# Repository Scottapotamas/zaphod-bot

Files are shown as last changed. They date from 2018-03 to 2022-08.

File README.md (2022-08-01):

# ZaphodBot Lightpainting Robot

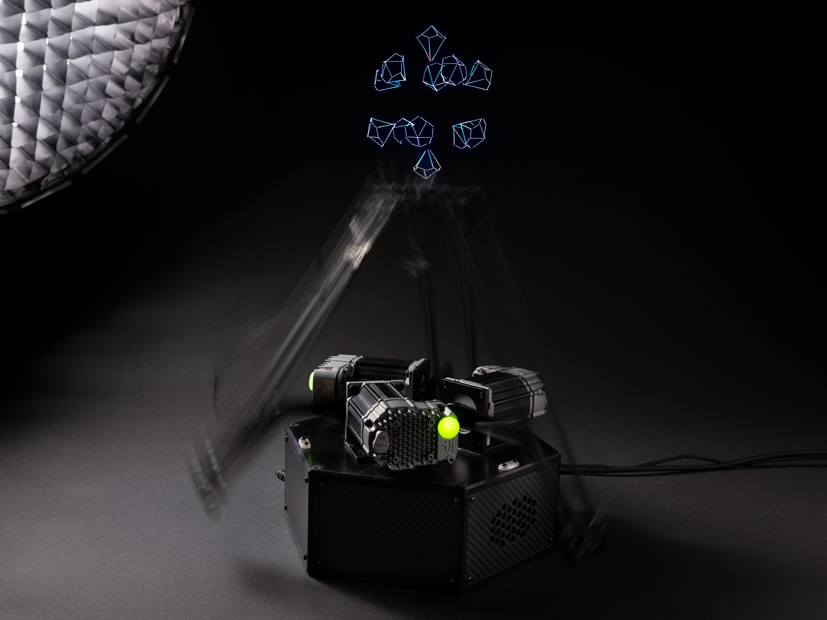
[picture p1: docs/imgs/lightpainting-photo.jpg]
lightpainting-photo


ZaphodBot is a DIY, 'high-end' rotary delta robot designed primarily for high-fidelity light painting.

It's served as a personal project where the majority of mechanics, electronics, firmware and higher level software has been designed from scratch (because why not).

I've detailed the design motivation and build in a more [longform post here](https://electricui.com/blog/delta-bot).

## Mechanics

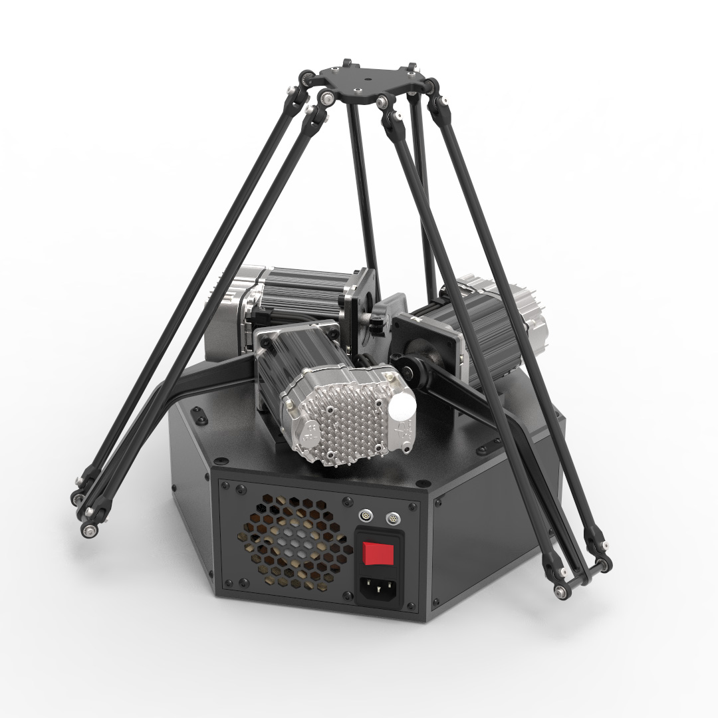
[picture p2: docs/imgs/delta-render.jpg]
Render of V1 Delta Hardware


CAD files for the robot are in Solidworks 2015 format, and can be found in `/mechanical/design/`.

The power supply and main electronics stacks live inside the hexagonal structure which forms the base, with servos mounted on top, connected directly to the arms.

To manufacture parts, see `/mechanical/design/manf_outputs/`  for drawings, STEP/DXF files. SLA 3D printing was used for joints, and CNC machining for the aluminium parts and carbon plates. 

All fasteners are standard metric hex bolts, with the exception of some bottom mounting holes which are 1/4in and 3/8in threaded holes to suit typical camera tripods.

## Electronics

The PCB was designed using KiCAD 5, located in `electronics/zaphod-controller`. Gerber outputs are available with BoM, but minor design revisions are needed to improve wire-loom layout and debug/expansion connector positions. 

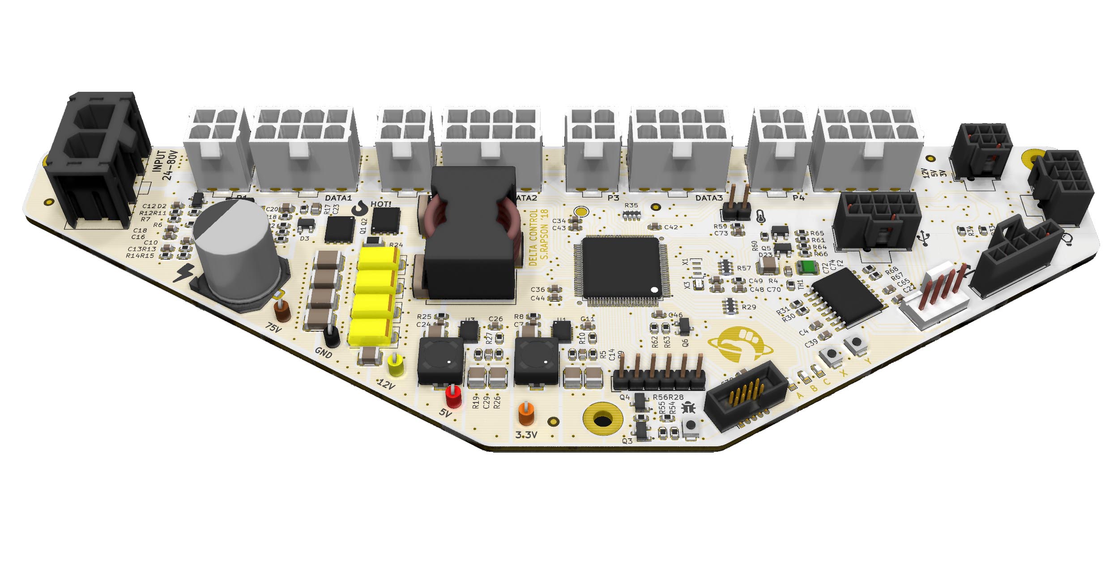
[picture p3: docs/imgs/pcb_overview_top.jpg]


It's based on a STM32F4 processor, provides regulated 3/5/12V from the 75V system supply, and manages the servos, internal IO and external IO.

- Power input (75V from Teknic IPC) through 2-pin MOLEX SABRE connector.
- Clearpath servo motors connect with 8-pin MOLEX MicroFit for signalling, and 4-pin MicroFit for 75V supply.
- Internal IO NanoFit connectors provide PWM fan support, UART, I2C, 2x ADC/DAC, and PWM. These can also be used as generic IO. See  `/electronics/zaphod-controller/Outputs/zaphod-controller-sch.pdf` for pinouts.
- Internal IO 2.54mm header strip provides switchable+fused 3.3V and USART, intended for wireless comms backpack in the future (likely ESP32 flavoured).
- The 9-pin LEMO connector used for external expansion provides galvanically isolated USB and 4 isolated IO lines (2 inputs, 2 outputs). Pinout in `/docs/connectors_pinouts.md`.
- The 7-pin LEMO connector supports a 4th Clearpath SD series servo, intended for use with rotating or linear stages. Pinout in `/docs/connectors_pinouts.md.`

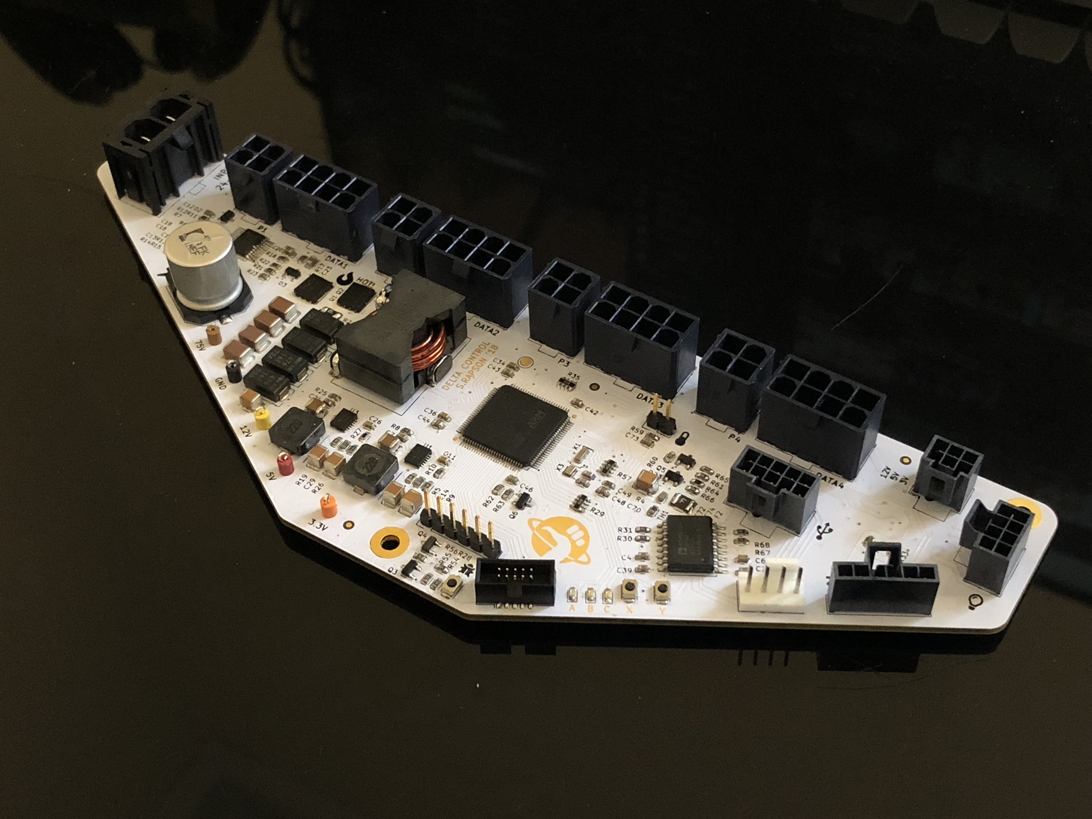
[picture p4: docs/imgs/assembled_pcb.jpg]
Assembled PCB


## Firmware

Microcontroller firmware (STM32) is in `/firmware`, is written in C, and can be built with a fairly standard `arm-gcc-eabi-none` toolchain.

I've used (and included config for) CLion as my main IDE, which is CMake based, though building with SW4/Eclipse shouldn't be too hard either.

Flashing the microcontroller is pretty standard as well, a 10-pin ARM CORTEX SWD socket is on the PCB, which connects to a STLink, Blackmagic Probe, or JLink programmer (used all three at various stages of this project).

# User Interface

The user interface is built with [Electric UI](https://electricui.com/install), and can be built and run by invoking `arc start` from `/interface`. 

It facilitates control and monitoring of the hardware, along with toolpath generation, optimisation and visualisation pipelines.

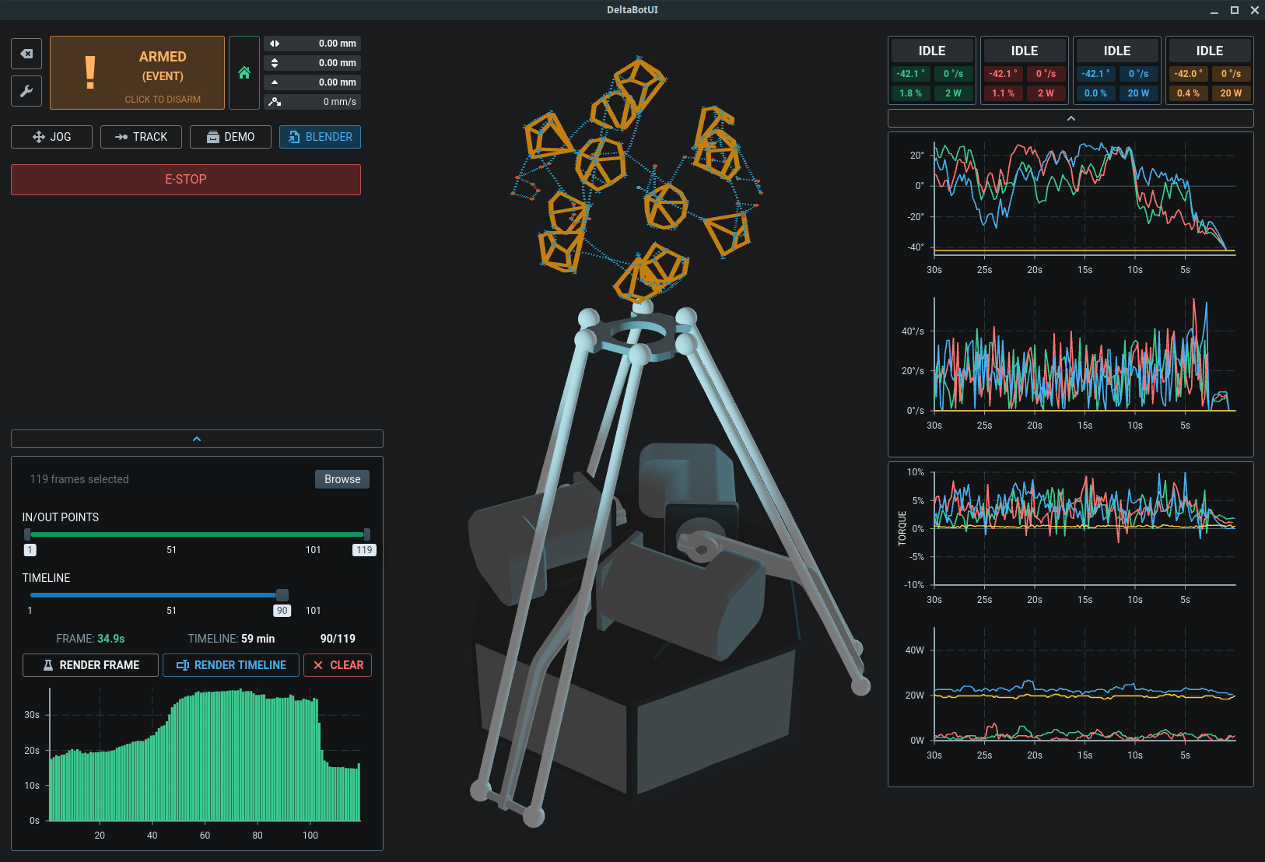
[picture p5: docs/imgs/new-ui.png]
User interface


## Toolpath Generation

Toolpaths for lightpainting are created by exporting spline data from [Blender using a Python script](https://github.com/Mike-Dax/total-perspective-vortex/blob/main/blender/addons/total_perspective_vortex/tpv.py), and loading the output with the "Blender" tab in the UI.

The frontend UI is responsible for parsing the Blender scene and performing a series of move planning and TSP optimisation steps to reduce render times.

https://user-images.githubusercontent.com/460325/182141536-1118c95f-b80b-4199-9833-aa961b41ea9a.mp4

> This screencap shows a Blender animation being loaded: the 'fast' plan completes within a second, then the multi-threaded TSP solver iterates on each frame to refine the path taken to render the particles.

# Accessories

## Light Painting

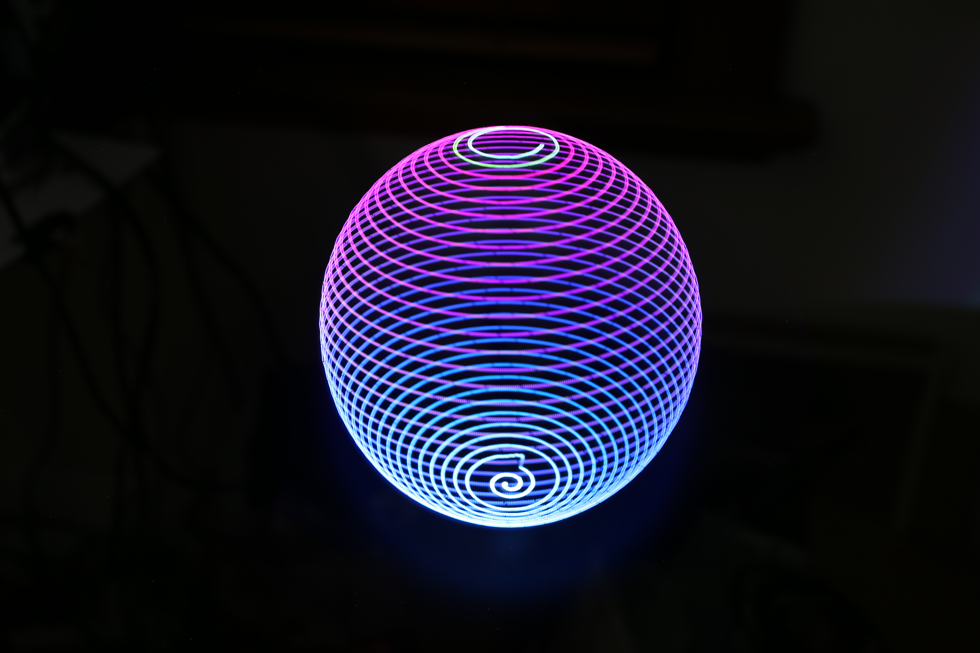
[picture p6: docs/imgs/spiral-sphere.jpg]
Light-painted spiral sphere


The light-painting 'brush' uses acrylic 1mm core fibre, connected to a 3x3W RGB LED.

The fibre is mounted to the effector with a turned acetal stalk (not documented), or with one of the SLA printed mounts found in `/mechanical/fibre-couplers/`.

The driver PCB is in `/electronics/rgb-led-board/` along with manufacturing files and a simple Arduino test program. This board connects to `zaphod-controller` via the 8-pin NanoFit connector, which provides PWM+IO and power.

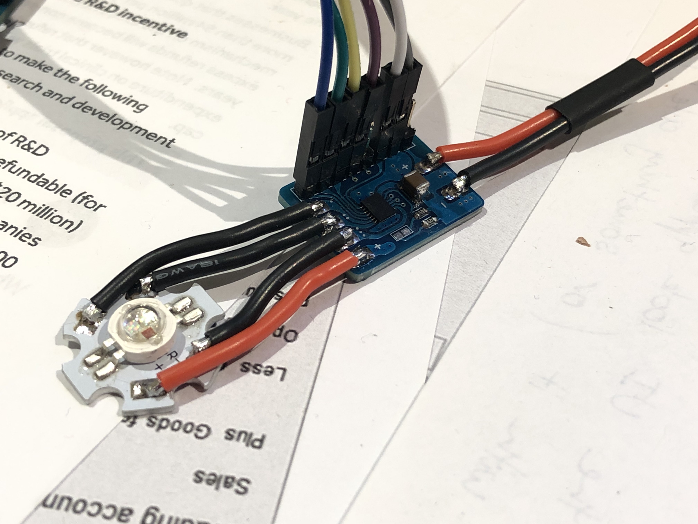
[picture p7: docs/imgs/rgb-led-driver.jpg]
RGB LED driver


## External E-STOP + IO Breakout Box

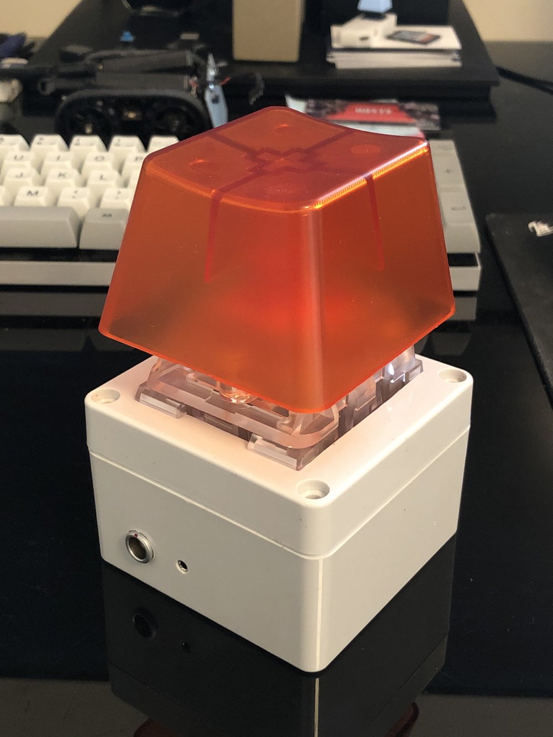
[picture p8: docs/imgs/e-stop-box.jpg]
E-STOP Box


The 9-pin LEMO connector is used with a 2m cable, connecting to the breakout box via matching 9-pin LEMO. A [Novelkeys Big Switch](https://novelkeys.xyz/products/the-big-switch-series) is used as an E-STOP, with the keyswitch light indicating motor state.

A 2.5mm stereo socket mounted in the box provides support for camera shutter release cable, in this case for a Canon N3 connector.

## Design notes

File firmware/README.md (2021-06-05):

# Embedded Firmware Readme

STM32F4 firmware for the zaphod-controller PCB. Manages the delta's servos and handles movement processing.

Uses the ST LL (LowLayer) hal as a base, with my own HAL on top of (or replacing) as applicable. Written for the STM32F429VET6 target microcontroller.

General system runs with event driven HSM design patterns, while background tasks use somewhat simple statemachines to handle operation.

## Building

Uses the `arm-gcc-eabi-none` toolchain, should build with fairly standard flags.

The external deps `electricui-embedded` and `electricui-interval-sender` use git submodules, and are both CMake aware.

`clang-format` config file is under git, used to maintain some semblance of style consistency.

GitHub Actions workflows are setup to build firmware in debug mode on commit to master, and release builds when tagged. Look at the Releases page on GitHub for binary downloads.

## Flashing and Debugging

I use CLion as my IDE alongside a JLink.

Depending on the version, either run a remote GDB server, or use CLion's integrated support.

### Manually running GDB server

Run the JLinkGDBServer as the remote GDB server instance with 

`./JLinkGDBServer -if SWD -device STM32F429VG`

then in CLion, connect with a remote GDB debugger with target-remote args of `tcp:localhost:2331`.

I had to edit my `~/.gdbinit` to include flashing and reset commands, which looks something like this:

```
# Reset the chip to get to a known state.
define target hookpost-remote
load
monitor reset
monitor halt
b main

# Set auto JTAG speed
monitor speed auto
```

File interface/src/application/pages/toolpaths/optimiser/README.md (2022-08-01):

# Colors

All colors are unit colours internally, RGB 0-1 values.

# Materials

Materials can't have any effect on the ordering of the movements.

## Blender Materials

Materials support arbitrary data transfer. Any `Object Data` custom properties
with the prefix `material.` will be transfered into the `material` entry without
the prefix. We use the `Object Data` custom properties because that usually
makes more sense with the object. GPencil and Lights are supported

Eg: to use the rainbow colour:

`material.type`: `rainbow`

Or a regular colour material

```
material.type: color
material.color: [1.0, 1.0, 1.0, 1.0]
```

Python syntax dicts can be entered for complex data structures

```
{'type': 'color', 'color': [1.0, 0.087, 0.05]}
```

Dot notation string keys can be used to override specific members (for use with
drivers)

```
material.foreground = {'type': 'z_depth', 'color_from': [1.0, 1.0, 1.0], 'color_to': [0.0, 0.0, 0.0], 'depth_from': 950, 'depth_to': 1000}
material.foreground.color_from = [0,0,1]
```

{'type': 'z_gradient', 'z_from': 105, 'z_to': 180, 'color_from': [0.360784,
0.145098, 0.360784], 'color_to': [0.760784, 0.454902, 0.760784]}

## Empty special data export

Custom properties of empty objects with the prefix `frame.` are exported, minus
the prefix, into the frame metadata store.

`frame.exp_angle` for example becomes `exp_angle` which is used to control the
4th axis.

## Drivers

Any property can be 'driven' by any combination of math, python scripting, and
other properties.

Right click -> `Add Driver` to add a driver.

# TODO:

- DRY the threejs representation into a simple colour interpolator
- BlendMaterial that can operate over two materials, multiply / min / max
- Z Fade material that fades 0 - 1 based on distance to camera near and far
- Fuzz material that can vary lighting intensity
- Some way to multiply light intensity with speed

- Motion fuzziness?

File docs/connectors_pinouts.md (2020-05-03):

# Connectors and Looms

General overview of components required for power delivery and signalling.

The main PCB will provide distro and sensing (voltage & current sense per motor) as well as IO connections.
This should hopefully keep the wiring neat and professional (looking, at least).

I'd like to sleeve each wire/bundle as well, but we'll see how much time I have.

# Mains Input Connection

Connect output of holder to IPC-3/5 PSU.

### Parts

- IEC320 Connector 	- Fused with DPST switch (no backlight). 
- Spade Terminals	- Female, fully shielded terminals. 
- Ring Terminal 	- for grounding connection(s). 
- 240IEC320V Fuse 	- M205 Quick Blow Fuse 4A. 

https://www.jaycar.com.au/iec-fuse-chassis-male-power-plug-with-switch/p/PP4003
https://www.aliexpress.com/item/AC250V-10A-2pin-ON-OFF-Rocker-Switch-IEC320-C14-Inlet-Socket-Single-Fuse-red-Switch-black/32861211516.html

Spade crimps - Potentially dubious quality, but better than the unshielded ones I have on hand...  
https://www.aliexpress.com/item/Lowest-Price-30PCS-Yellow-red-blue-Splice-Wire-Connectors-Insulated-Male-Female-Crimp-Spade-Terminals-18/32764325209.html

### Wire

Preferably in black insulated (round):

- 2.5mm^2		Blue
- 2.5mm^2		Brown
- 2.5mm^2		Green/Yellow

### Pinout

- Active is connected directly to the fuse holder on the IEC connector. 
- Connect the fused active to the switch. 
- Connect the switched active to the IPC active connection. 
- Neutral directly to IPC neutral pin. 
- Earth directly to the IPC neutral pin. 

# Teknic IPC-3/5 Open Frame PSU

## Mains Input connector

Connect to input protection circuit(s).

### Parts

- Molex MiniFit-Jr 	8-Way - 39-01-2080
- Molex MiniFit-Jr	Crimp - 39-00-0039

### Wire

From IEC switch unit (2.5mm^2 3-core).  
This was cut from an older black 240-IEC cable.

### Pinout

- Pin 1-4 	No Connect for 230V, read manual for 110V operation
- Pin 5 		AC Active
- Pin 2 		Earth
- Pin 2 		Earth
- Pin 8 		AC Neutral

## 75 Output Connector

- Connect IPC-3/5 Output to main PCB.  
- The PSU and the PCB use common connector and pinout.
- This is also listed in the Teknic IPC User manual PDF.

### Parts

- Molex Sabre 		2-Way - 44441-2002 
- Molex Sabre 		Crimp - 43375-0001

### Wire

- 14-16AWG 	Red
- 14-16AWG 	Black

### Pinout

- Pin 1 		VCC
- Pin 2 		GND

# Teknic Clearpath Motor(s)

I bought ModDIY pre-crimped mini-fit cables to reduce the labour of individually sleeving these.  
In hindsight, I should have provisioned a panel mount connector for the top plate, and had the full looms made up (including connectors) as the ModDIY cables had thick heatshrink that interferes with insertion into the housing, taking as long/longer than full DIY cables...

## Power Connector

- Connect motor power to the main PCB.
- Motor and PCB share common pinouts, connectors etc.

### Parts

- Molex MiniFit-Jr 	4-Way - 39-01-3045
- Molex MiniFit-Jr 	Crimp - 39-00-0078

https://au.rs-online.com/web/p/pcb-connector-housings/6704575/  
https://au.rs-online.com/web/p/pcb-connector-contacts/2155887  

### Wire

- 16AWG 		Red
- 16AWG 		Black

### Pinout

- Pin 1 		VCC
- Pin 2 		GND
- Pin 3 		VCC
- Pin 4 		GND

## Control Connector

- Connect clearpath data connector to main PCB.  
- Motor and PCB share common pinouts, connectors etc.  

### Parts

- Molex MiniFit-Jr 	8-Way - 39-01-3085
- Molex MiniFit-Jr 	Crimp - 39-00-0078

https://au.rs-online.com/web/p/pcb-connector-housings/8428197/
https://au.rs-online.com/web/p/pcb-connector-contacts/2155887

### Wire

- 22AWG 		Blue
- 22AWG 		White

### Pinout

- Pin 1 		HLFB+
- Pin 2 		Input B+
- Pin 3 		Input A+
- Pin 4 		Enable+
- Pin 5 		HLFB-
- Pin 6 		Input B-
- Pin 7 		Input A-
- Pin 8 		Enable-

The PCB connects the + signals to the common 12V rail, as signalling is done on the low side.

# Expansion LEMO Connectors

## Data Connector

Allows for user-domain expansion of USB and some generic IO (UART, CAN, 2x input, 2x output).

### Parts

LEMO 0B 9-pin

Socket: EGG-0B-309-CLL
https://au.mouser.com/ProductDetail/LEMO/EGG0B309CLL

Plug: FGG-0B-309-CLAD-52Z
https://au.mouser.com/ProductDetail/LEMO/FGG0B309CLAD52Z

As a pair (off-brand equiv): 
https://www.aliexpress.com/item/LEMO-connector-EGG-0B-309-CLL-FGG-0B-309-CLAD-Z-31Z-42Z-52Z-LEMO-connector/32318767655.html

### Wire

USB3		Black Sheath

Usb cable provides 9 usable conductors (not counting the shield), with good shielding, and compatible diameter with lemo sheath.

Black glue-lined 6mm heatshrink was used to protect the joints on the panel mount side.

### Pinout

When looking at the back side of the LEMO panel mount connector (wire side), with the alignment notch facing up.
The pin pattern is defined where pin 1 is the pin directly underneath the alignment notch, counting upwards in a counter clockwise direction, and pin 9 is the centre pin.

```
     1      
  2     8   
 3   9   7  
  4     6   
     5     
```

'Legacy' USB FS Connection:

- Pin 1 		GND 	BLACK
- Pin 2 		D+		GREEN
- Pin 3 		D-		WHITE
- Pin 4 		5V		RED

IO Group 1 (CAN Capable):

- Pin 5 		In/RX	BLUE
- Pin 6 		Out/TX 	YELLOW
- Pin 9 		IOGND	BARE (in pair shield)

IO Group 0 (UART Capable):

- Pin 7 		In/RX	PURPLE
- Pin 8 		Out/TX 	ORANGE
- Pin 9 		IOGND	BARE (in pair shield)

IO and USB don't share ground. The two IO groups share ground cores as the PCB joins them anyway.

### Notes

- The USB3 insulation diameter just fits inside the LEMO strain relief jacket. This required a bit of force, and some slight lubrication of the wire.
- The USB Shield connection (outer copper core, and woven+foil shield) was not electrically connected at the lemo plug/socket side.
- Hot air gun was used to slightly soften the panel-mount -> PCB loom to allow bending. These bends are reasonably well retained after cooling.

## Motor Connector

Allows for addition of an external clearpath motor (or something that uses the same IO style)

### Parts

LEMO 0B 7-pin

Socket: EGG-0B-307-CLL
https://au.mouser.com/ProductDetail/LEMO/EGG0B307CLL

Plug: FGG-0B-307-CLAD-52Z
https://au.mouser.com/ProductDetail/LEMO/FGG0B307CLAD52Z

As a pair (off-brand equiv): 
https://www.aliexpress.com/item/LEMO-connector-EGG-0B-307-CLL-FGG-0B-307-CLAD-Z-31Z-42Z-52Z-LEMO-connector/32318771454.html

### Wire

N/A

### Pinout

```
  1     6   
 2   7   5  
  3     4   
```

- Pin 1 		75V 	RED
- Pin 2 		12V		BROWN
- Pin 3 		ENABLE	BLACK
- Pin 4 		A		BLUE
- Pin 5 		B		GREEN
- Pin 6 		HLFB 	ORA
- Pin 7 		GND 	YELLOW

### Notes

- The 7-pin connector was selected for unique pin count, higher supported wire gauge (and higher per-pin current).
- Not intended for continuous high power delivery to motors, mostly for use with rotation or belt surfaces, or possibly rail drive.
- Connector pins are rated at 2.5A continuous.
- Isolation rating of connectors is >700V, therefore 75VDC is fine.

# Expansion Temperature Probe

Used for temperature sensing off the main control board. 

Recommended location is inside the warmer area of the IPC-3/5 PSU to allow for automatically moderated airflow.

### Parts

10K NTC Thermistor  
https://www.aliexpress.com/item/10K-Precision-Epoxy-Thermistor-3435-NTC-Pack-of-2/32819250168.html

2-pin 2.54mm pitch 'DuPont' connector

I sleeved and heatshrinked over the plug. The thin nylon wires were a pain to manage.

### Wire

Thermistor already comes pre-wired.

### Pinout

It behaves as a resistor, pinout doesn't matter. 

Crimp both terminals into the 2-pin socket, connect to temp header on PCB.

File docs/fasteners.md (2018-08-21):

# Version 1 Fasteners

## Bearings

4mm ID, 4mm depth, 9mm OD

Instead of paying $5 each (x24), I found some on aliexpress

https://www.aliexpress.com/item/Free-Shipping-10-PCS-S684ZZ-Bearings-4x9x4-mm-Stainless-Steel-Ball-Bearings-DDL-940ZZ/32835314182.html

Bearings seem of reasonable quality, centre retainer is slightly looser than I'd like.

## Shoulder bolts

There are two shoulder lengths required, 4mm for effector and bicep connections, and 8mm for use with the clevis links.

I went with the cost effective aliexpress option https://www.aliexpress.com/item/10pcs-M3-thread-4mm-stainless-steel-304-shoulder-screw/32861370400.html

4mm and 8mm skews were purchased.  
They seem dimensionally undersized for the shoulder diameter (3.85-3.92mm shoulder).  
Hex head forming seems a bit rough.   
Otherwise seem ok though.  

### Steel slotted variant

4mm shoulder, 4mm shoulder length, M3x0.5
4.5mm thread length
Carbon steel

SHLD040-004-SLL-C - $1.95AUD each

https://www.minibearings.com.au/store/item/shld040004sllc/

### Stainless Hex variant

4mm shoulder, 4mm shoulder length, M3x0.5
303 Stainless Steel
4.0mm thread length

SHLD040-004-SKT-S3 - $3.95AUD each

https://www.minibearings.com.au/store/item/shld040004skts3/

### Stainless Hex variant

4mm shoulder, 8mm shoulder length, M3x0.5
303 Stainless Steel
4.0mm thread length

SHLD040-008-SKT-S3 - $3.95AUD each

https://www.minibearings.com.au/store/item/shld040008skts3

# Version 2 Mechanism

The version 1 mechanism has way too much slop due to poor tolerances in the bearings and shoulder bolts. Good lesson in not trusting Aliexpress fasteners...

This set will use higher quality fasteners from Misumi, but requires a few parts to be reprinted.

## Bearing Retaining Posts

Without re-machining or redesigning the elbow spacer part, I'm limited to a M3 thread.

The "Bearing Shaft Screws with Retaining Rings - Flanged" look pretty good, https://sg.misumi-ec.com/vona2/detail/110300115260/
or a simpler option that don't have a retainer (basically a shoulder bolt) https://sg.misumi-ec.com/vona2/detail/110302644720/

The M3 thread size in these categories locks us into a 5mm diameter which drives bearing selection.
Its got a 6mm thread length, and 8mm head

## Bearings

Inner Diameter: 5mm
Outer Diameter:	11mm
Width:			5mm

The misumi branded stainless steel shielded bearings https://sg.misumi-ec.com/vona2/detail/110302273360/?HissuCode=SB685ZZ look like a good option. Its 3.60USD at qty 26 (need 24 + 2 spares) 

94.64USD.

## Clevis Bearing Pin/Shaft

TBD, misumi have poor selection of ~10mm options, most start at 15mm shank which isn't ideal.

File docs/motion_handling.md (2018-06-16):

# Motion Handling

Summary of the motion planning setup.

## Work Area

The main co-ordinate system is represented as a cartesian space, measured in microns. This allows for use of int32 x, y, z numbers with sufficient resolution and spare room for rails etc.

The XY plane is defined as the plane parallel to the main hexagonal plates of the delta, with the 0-point of XY being co-linear with the central vertical axis of the bot (centre of plate, motor axis etc). The Z axis is defined as the vertical distance from the delta, where the '0' position is the closest reachable point to the delta's base electronics assembly (i.e. arms are about to hit endstops). Positive Z positions are away from the robot, moving towards the fully extended range of motion.

## Motion Processing Pipeline

Movements can be specified as one of several types, a transit, line, or one of several spline choices (catmull rom, quadratic bezier, cubic bezier). 
Points are passed to the pathing engine to generate the lines or splines, in micron-resolution x,y,z cartesian format.
A 'target duration' is specified for the movement, where the delta will attempt to complete the move by the elapsed duration.

While executing a movement, the pathing engine will calculate the time elapsed since the start, and calculate the percentage of completion required.
The end-effector's position is calculated using the appropriate line or spline interpolation function, with the percentage as the dependant variable.
The output co-ordinates are then fed into the kinematics driver, which performs the inverse kinematics required to translate the cartesian co-ordinates into motor angles.
On successful IK solve, the motor angles are sent to the clearpath handlers, which convert the target position into steps, and manage the actuation of the servos.

By repeating this process often, movement along a path can be achieved with some level of accuracy (assuming the servo motors can maintain control to meet the setpoint).
As the processing stages require a non-zero amount of compute time, the number of 'subdivisions' achieved by the pathing engine is dependant on the time allowed by the movement.
Therefore, large fast moves have lower resolution than either smaller fast moves, or large slow moves.

## Servo Angles

When the servo homes, it moves to an endstop which correlates to a bicep angle of -65° (where 0° is parallel to the plate). 
The motor then moves 150 steps from this point as a 'buffer', or to -56.5°.

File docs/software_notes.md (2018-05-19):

# Architecture Overview

There are a few layers of abstraction which make up the overall structure of the firmware.

| Folder 				| Description  	|
|---				|---			|
| app_state_machines 	| HSM structured higher level logical tasks. Subscribe and emit events. Only allowed to interact with drivers. 										|
| drivers 				| Simpler self-contained modules, some contain a simple-state-machine implementation. Typically manage hardware, convert sensors to quantities etc.  	|
| hal 				| Hardware abstraction to interact with specific peripherals or microcontroller functions.  															|
| utility 				| Helper code which forms the backbone of the statemachines, or some other generic behaviour (fifo, queues, state machine macros).  					|

The hal layer provides convenience wrappers for other lower level functionality, be it direct register calls or interfacing with the STM32 HAL layers.

The intent of 'my' hal layer sitting above the STM32 HAL is to further decouple the code from the STM ecosystem, which improves testability and reuse of drivers.

## Tasks (HSM)
 
Based on a hierarchical state machine structure (HSM), which provides event-driven state machines called 'tasks'.  
Found in /src/app_state_machines

Event timers are evaluated on a tick timer (along with ADC or other timing specific modules).  
The main loop sleeps wherever possible, waking on interrupt. At this point, the background processors are visited, then a task from the queue is run.  
For a given 'task', an arbitary number of states can be defined (as functions), which contain a macro driven pattern for handling entries and exits from the state, and handling for external events.

## Drivers
 
Simpler blocks designed to operate statelessly or with a simple state machine and processing loop. These aren't handled by the task systems, and aren't intended for complex logic.
Found in /src/drivers

Drivers should expose public facing functions for init, getters and setters, and processing 'loops' if required.  
A driver will typically perform a role where interaction with the HAL layer is required, such as sampling a ADC, i2c sensor, or drive a PWM output, and typically provides human-friendly interactions with the underlying hardware.  
ADC or sensor readings should be converted into a SI unit for example, and averaging/bounds/error detection should be done at this layer.

## hal

Interacts with the hardware on a more generic level. This may be direct hardware register manipulation, or calls to a vendor HAL codebase.  
Found in /src/hal   

hal code should strive to abstract the operation of the bare metal to simplistic actions such as start/stop/action, and should attempt to consolidate settings for peripherals.  
This is designed to allow the driver layers to be unit tested independantly of hardware, as the hal layer can be mocked.  
Also promotes portability as the hal layer can be changed subtly for new vendor IC's as needed.

## utilities

Provides standard functionality used across driver or task layers, includes functionality like queuing, state handling or buffer style functions.
Found in /src/utilities  

Many modules consist of defines or macros to simplify the higher layer.  
Where possible, these are as generic as possible.

# Delta Notes

General overview/thoughts regarding firmware development for the controller. These might be as simple as listing the responsibility of certain modules.

## Fan Control

The fan driver presents a simpler loop run in the background at a lower-rate.  
Interacts with the hal PWM to set fan speeds, and monitor the fan hall sensor and temperatures.  

Handles starting/stopping the fan with a blip to higher speed to ensure safe starting.  
Includes stall detection and underspeed detection, attempts to restart.  
Monitors the temperature and tracks a fan curve for auto-speed.  

## Kinematics 

The kinematics driver provides transforms between the cartesian co-ordinate space, and angular roations for each motor.

Forward Kinematics (angles to position) and Inverse Kinematics (position to angles) are available.
Functions take a structure for either position or angles as input, with a pointer to a writable structrure (output) of the other type.

Bypassing this module would allow use of the overall motion planners etc for different mechanisms (SCARA, cartesian, etc)

## Path Interpolator

Driver operates in the cartesian domain only, and is designed to accept a 'motion request' and then execute the motion over some duration of time.  
As movement to a destination isn't as simple as driving motors to the final destination instantly (co-ordination is required for correct temporal profiles, kinematics considerations etc), we need to calculate a target position for the end effector at a given time, then calculating the intermediary movements to provide speed/duration control etc.  

To ensure the effector follows the target profile over time, the motion is broken up into smaller chunks. Greater number of chunks provides greater adherance to the intended profile.  
As the delta is intended for use against temporal problems, the movement engine was designed around the concept of 'time domain' movement execution, not feed rate based moves like many CNC machines.  

As such, each movement has a corresponding 'duration', and the interpolator driver strives to complete the movement within this time window.  
By adjusting the rate of the interpolator's loop, the fidelity of the movements is then traded against movement speed.  
A large and small movement which share execution durations will recieve a similar number of chunks, and therefore positional adherance will vary.

Tool-positioning calculations depend on the style of motion requested, and several interpolation functions are included to assist with this:

### Transit movements

Transit movements are used where the 'where' matters more than the 'how', and will execute without any guarantee of the tool path between points.

For the delta, the end effector position along this transit move will be influenced by the non-linear relationship of the mechanics and motor angles.

### Line Movements

Linear interpolations are used to perform line following between 2 3D points.

### Spline Movements

Catmull-Rom Spline interpolations are used to follow a segment of the curve defined by 4 points.

https://en.wikipedia.org/wiki/Centripetal_Catmull-Rom_spline

The higher level task, or the movement generation tool can generate large chains of points to ensure all waypoints are hit.

### Arbitary Equation Moves

Not currently implemented.

The ability to accept an arbitary mathematical function is a wanted feature? 
Could be cool to provide arbitary spirographic functions for demos.

## Clearpath Driver

Handles the homing and control of a single servo.
Monitors current and feedback pins to approximate some failure detection/prevention.

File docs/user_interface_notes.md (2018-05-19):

# Delta Robot User Interface

General musings and tracking of user interface development.

## Overall System

| Group 	| Component 	| Task 	| Implemented 	|
|---	|---	|---	|:---:	|
| Fan Control  	| Speed % 	| Show current duty cycle 	| 	|
| 	| Speed RPM 	| Show current RPM 	| 	|
| 	| Fan Curve 	| Allow edits of temp/speed curve 	| 	|
| Temperatures 	| PCB Ambient 	| In open-air part of PCB 	| 	|
| 	| PCB 12V Reg 	| Underneath 12V regulator 	| 	|
| 	| External Probe 	| Flying probe (near 75V PSU) 	| 	|
| Motion 	| Status 	| Idle, homing, transit, line, spline, etc  	| 	|
| 	| Cartesian Pos 	| (X, Y, Z) in 20.05mm format 	| 	|
| 	| Angular Pos 	| Shaft angles in 34.5° format 	| 	|
| Status 	| System State 	| Overall hardware status 	| 	|
| 	| LED 0 	| Indication matching onboard leds 	| 	|
| 	| LED 1 	| 	| 	|
| 	| LED 2 	| 	| 	|
| 	| Button 0 	| State of button presses (accept UI press) 	| 	|
| 	| Button 1 	| 	| 	|
| 	| CPU Load % 	| Utilisation Stat 	| 	|
| 	| Micro Core Temp 	| Internal temperature sensor 	| 	|
| 	| Add-in card state  	| If add-in card is powered or not 	| 	|
| 	| Buzzer state 	| If buzzer is currently indicating or not  	| ? 	|
| Motor X 	| State 	| Passive, Homing, Idle, Motion, Error 	| 	|
| 	| Feedback Signal 	| -100% to +100% value for velocity/torque  	| 	|
| 	| Current Position 	| Internal tracked current position 	| 	|
| 	| Target Position 	| Servo driver target 	| 	|
| 	| Power 	| Consumption in Watts 	| 	|
| 	| Current 	| Draw in 1.25A format 	| 	|
| 	| Current Fault Flag 	| Indication from sense IC of OC event 	| 	|

# UI Components required

The UI will require the following generic data driven components:

- Graphs (continuous display of live values).
- Statistics/Labels of data.
- Indicator 'lights' for button and status led indication.
- Fan curve viewer/editor.
- State Indication (text mapper from int -> strings).
- Notifications/alerts
- Mode Selection Module.
- Emergency stop button.

- Visualiser of end effector position/trail in cartesian space.
- Visualiser of delta mechanism with movements (either do IK or FK at UI side).

These elements will require grouping to improve readability, and dropdowns, tabs or navigation required to expose all information.

For example:

- Dropdown/tab in isolated box to select between motor overviews, and Servo 1-3 detail status.
- Grouping of status values, temperatures and state information.
- System stats like CPU load and microcontroller core temperature on a separate page or footer element.

Some states will flag critical issues or confirmations, and these should require either an OS level notification, in-app banner, or challenge dialog.

## Mode Selection Module

Allow selection between operation modes: Manual control, demo sequences, run program, accept serial

### Manual Mode 

Direct user input of motion controls.  
Suggest ability to toggle which input method is used:

- UI entry (sliders/buttons that fire a fixed amount of movement per press).
- Mouse/touchpad control (xy control in a box).
- Joystick control (bluetooth or connected gamepads).
- Spacemouse Control (attached to the UI/host computer).
- Manual entry of position as x,y,z fields, in mm.

### Demo Mode

Run through preset motion demos to show off the control accuracy and velocities of the delta.

Concepts include:

- Tracing out simplistic 2D geometry.
- Trace out 3D cube edges.
- Spiral and cone style patterns.

### Program Mode

UI presents interface for file selection.  
Either microcontroller stores the file, then runs, or the UI feeds motion commands piecemeal.  
Shows progress indication bar.  

### Serial Mode

Accept control inputs from external connection and other devices.  
This allows the UI to be used as a supervisor.

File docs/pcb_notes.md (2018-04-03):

# Main Interface PCB

Purpose: Accept inputs, provide output connectors, maintain wiring and provide high level control over system.

Side Goals: Look awesome.

# Requirements

## Input

- Accept 75V DC from IPC-3 PSU with 2-pin Molex SABRE connector.
- Minimalistic input protection and filtering as supply is trustworthy.
- Polyfuse, a few caps for stability?
- Input voltage test points

## Processing

- Accept input position data at high rate (USB, Ethernet, Wifi, SD/USB are all acceptable).
- Drive 3 stepper motors at high speed, i.e. maximum achievable square waves for ultimate positioning control
- Drive 1-n RGB LEDs for output
- External optocoupled IO for inputs/soft stop switch, and camera trigger events.
- Should be able to handle reasonably involved trig/floating point maths for kinematics calculations.
- External outputs for end affector upgrades in the future
- Inputs for homing switches
- Buzzer output for safety alerts?

## General nice-to-haves

- Onboard NTC for temperature monitoring
- Expansion NTC's to monitor IPC-3 power supply temperature, etc.
- PWM Fan output for cooling
- Consider input voltage, and current sensing on each servo output rail.
- SWD Connection with ARM CORTEX 5x2 pin female 1.25mm pitch.
- Ensure high reliability, robust IO and isolate where practical.
- Expansion PWM outputs for end affector upgrades/changes in the future (pumps/servos etc)
- Expansion UART and/or CANBUS for external interfacing.
- Terminal over UART is nicer than USB for debugging.
- Testpoints for scope/function generator
- TTL level lines could use 2.54mm 4x2 connectors for Saleae logic analyser connection (step+dir+enable+hlfb).
- Consider onboard RTC battery connection.
- Connection for ESP8266/32 for wireless expansion?

- Matte-black PCB with ENIG finish. Gold text etc.
- Use only Orange or Blue LEDS for indication
- Leds should be low brightness or include disable functionality.

## Outputs

- 3x Motor Connectors (power + control connectors)
- Status/state LEDS on important pins for visual debugging.
- External UART
- External USB
- External IO

- Bonus for 4th motor output if 4th axis expansion is considered

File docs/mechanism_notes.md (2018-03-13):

# Delta Mechanism Design

Goal is for a high speed, high resolution, low load actuator in 3-dof space.

- Ideally the platform has minimal visual occlusion from the end affector over the widest range of angles possible.
- Ideally the end effector is capable of moving at the same/similar velocities for any direction.
- The expected load on the end effector is not much heavier than some small electronics (sensor, LEDs, etc).
- The mechanism should operate while pointing up, and while hanging in a 'downwards' facing orientation.

## Mechanism Options

- SCARA (single arm)
- SCARA (parallel)
- Delta (linear)
- Delta (angular)
- Cartesian XYZ style approaches
- Multi-dof arm approach

Key metrics for selection are personal attraction (motivation is important), low effector mass, high velocities and resonably high positioning resolution/repeatability.

Cost and size of actuators is an important factor, mechanical simplicity of arms is somewhat important.

A delta was considered one of the best options, beating out SCARA and various COREXY/XZ designs on speed, form factor, and personal attraction to the design.

## Delta Design Notes

### General Notes

- Need to work out base size to package motors, electronics, power supply and other ancillaries. Ideally an IEC cable enters the base 'box' and little to no other lines are in/out if possible.
- Should be portable by a single person if possible (if not, add handles).
- Leave room for a higher end processor (Odroid or Raspberry Pi etc) for future expansion.
- Mounting points on sides and base for mounting to external motion control systems, support structures or feet for table use.
- Ideally the moving mechanism is vibration damped from any extenal mounts to reduce transmission of HF movements.

### Base, Arm Sizing

### End Effector

### External Mounting

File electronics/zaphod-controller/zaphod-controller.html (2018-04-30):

# BOM By Value

Source: F:\Projects\zaphod-bot\electronics\zaphod-controller\zaphod-controller.sch

Number of components: 231

Ref | Qnty | Value | Part | Description | PartNumber | Vendor
C1, C4, C7, C16, C22, C24, C37, C38, C39, C40, C41, C42, C43, C44, C46, C47, C50, C51, C52, C53, C54, C55, C65, C70, C71, C73, C74, C76, C77, C78, C79 | 31 | 100n_X7R_1608M | 100n_X7R_1608M | CAP, MLCC, X7R, 100NF, 50V, 0603
C10 | 1 | 15p_X7R_1608M | 15p_X7R_1608M | CAP, MLCC, C0G/NP0, 15PF, 50V, 5%, 0603, 1608M
C11, C12, C26, C34, C35, C36, C45 | 7 | 1u_X7R_1608M | 1u_X7R_1608M | CAP, MLCC, X7R, 1UF, 50V, 0603
C13 | 1 | 1n5_X7R_1608M | 1n5_X7R_1608M | CAP, MLCC, X7R, 1500PF, 50V, 10%, 0603, 1608M
C14, C29, C48, C49 | 4 | 22p_X7R_1608M | 22p_X7R_1608M | CAP, MLCC, X7R, 22PF, 50V, 0603
C15, C17, C31, C32, C33, C72 | 6 | 22u_X7R_3225M | 22u_X7R_3225M | CAP, MLCC, X7R, 22UF, 25V, 10%, 1210, 3225M
C18 | 1 | 330p_X7R_1608M | 330p_X7R_1608M | CAP, MLCC, X7R, 330PF, 50V, 0603, 1608M
C19, C20, C23 | 3 | 1u_X7R_2012M | 1u_X7R_2012M | CAP, MLCC, X7R, 1UF, 16V, 0805, 2012M
C2 | 1 | 47u_ELEC_100V_1350X1350M | 47u_ELEC_100V_1350X1350M | CAP, ALU ELEC, 47UF, 100V, 320mOhm, AEC-Q200, 5000 hour, SMD
C25, C27, C28, C30 | 4 | 47u_TANT_7343M | 47u_TANT_7343M | CAP, TANT, 47UF, 16V, 7343-31
C3, C21, C75, C80 | 4 | 10u_X7R_3225M | 10u_X7R_3225M | CAP, MLCC, X7R, 10UF, 25V, 1210 3225M
C5, C6, C8, C9 | 4 | 2u2_X7R_4532M | 2u2_X7R_4532M | CAP, MLCC, X7R, 2.2UF, 100V, 1812, 4532M
C56, C57, C58, C59 | 4 | 10n_X7R_1608M | 10n_X7R_1608M | CAP, MLCC, X7R, 10NF, 25V, 0603
C60, C61, C62, C63, C64, C66, C67, C68, C69 | 9 | 1n_X7R_1608M | 1n_X7R_1608M | CAP, MLCC, X7R, 1NF, 100V, 0603
D1, D6, D7, D8, D9, D14, D15, D16, D17, D18, D19, D20, D21, D22, D23 | 15 | BAV99 | BAV99 | DIODE DUAL, 100V, 215mA, 4ns, SOT23
D10, D11, D12, D13 | 4 | 3V3 | 3V3_500mW_SOD123 | DIODE, Zener 3V3, 500mW, SOD123
D2, D3 | 2 | 200V_350mW_SOT23 | 200V_350mW_SOT23 | CMPD2003C DIODE DUAL, Common Cathode, 200V, 200mA, 4A peak, 350mW, SOT23-3
D24 | 1 | LED_RED_1608M | LED_RED_1608M | DIALIGHT ChipLED Red, 0603, 1608M
D4 | 1 | LED_YELLOW_1608M | LED_YELLOW_1608M | DIALIGHT ChipLED Yellow, 0603, 1608M
D5 | 1 | LED_GREEN_1608M | LED_GREEN_1608M | DIALIGHT ChipLED Green, 0603, 1608M
F1, F2 | 2 | 0.5A_1210L_PTC | 0.5A_1210L_PTC | FUSE, RESETTABLE, PTC, 13.2VDC, 500mA, SMD, 1210L050
FB1, FB2 | 2 | 1K_1608M | 1K_1608M | FERRITE BEAD, 1Kohm @ 100MHz, 0.6Ohm, 100mA, 0603, 1608M
L1, L2 | 2 | 22u_MCSDRH73B | 22u_MCSDRH73B | INDUCTOR, 22UH, 1.83A, Shielded, 0.13ohm
L3 | 1 | 10u2_PA2050 | 10u2_PA2050 | INDUCTOR, 10.2UH, 12.5A, 10%, 0.0058ohm
LS1 | 1 | PKMCS0909E4000-R1 | PKMCS0909E4000-R1 | Murata Buzzer, passive, piezo transducer, 12V, 9x9x1.9mm, SMD, top firing
P1 | 1 | MOLEX_43160-0102 | MOLEX_43160-0102 | AS7.5mm pitch, Vertical, PTH, 2 contacts
P11, P12, P13, P14 | 4 | MOLEX_MINIFIT_JR_2x4_WAY | MOLEX_MINIFIT_JR_2x4_WAY | CONNECTOR, SOCKET, 8POS, 2ROW, MINI-FIT JR, 5566 series, 4.2MM pitch, PTH
P15 | 1 | MOLEX_NANOFIT_2x4_WAY | MOLEX_NANOFIT_2x4_WAY | CONNECTOR, SOCKET, 8POS, 2ROW, Nano-fit, 105310 series, 2.5MM pitch, PTH
P16 | 1 | MOLEX_NANOFIT_1x6_WAY | MOLEX_NANOFIT_1x6_WAY | PCB Socket, 2.5mm pitch, 105309 series, Vertical, PTH, 6-WAY, 1-ROW
P17 | 1 | MOLEX_NANOFIT_2x3_WAY | MOLEX_NANOFIT_2x3_WAY | PCB Socket, 2.5mm pitch, 105310 series, Vertical, PTH, 6-WAY, 2-ROW
P18 | 1 | CONN_01X02 | CONN_01X02 | Pin Header, 2.54mm, Vertical, PTH, 2 Way, 1 Row, 01x02
P19 | 1 | MOLEX_KK2.54_1x4_WAY_FAN | MOLEX_KK2.54_1x4_WAY_FAN | CONNECTOR, SOCKET, 4POS, 1ROW, KK 2.54, 2.54mm pitch, PWM fan header, PTH
P2, P3, P4, P5 | 4 | MOLEX_MINIFIT_JR_2x2_WAY | MOLEX_MINIFIT_JR_2x2_WAY | CONNECTOR, SOCKET, 4POS, 2ROW, MINI-FIT JR, 5566 series, 4.2MM pitch, Vertical PTH
P20 | 1 | CONN_01X06 | CONN_01X06 | Pin Header, 2.54mm, Vertical, PTH, 6 Way, 1 Row, 01x06
P21 | 1 | MOLEX_NANOFIT_2x5_WAY | MOLEX_NANOFIT_2x5_WAY | CONNECTOR, SOCKET, 10POS, 2ROW, Nano-fit, 105310 series, 2.5MM pitch, PTH
Q1, Q2 | 2 | Si7852DP | Si7852DP | MOSFET N-CH, 80V, 12.5A, 16.5mOhm, SOT-23
Q3, Q6 | 2 | 2N7002P | 2N7002P | MOSFET N-CH 60V 0.36A SOT-23
Q4 | 1 | NTR1P02T1G | NTR1P02T1G | MOSFET, P-CH, 1A, -20V, 0.148ohm, -10V, -1.9V
Q5 | 1 | BC847B | BC847B | Transistor, NPN, 45V, 100MHz, 250mW, 100mA, 250mW, SOT-23
R1, R2 | 2 | 130K_1608M | 130K_1608M | RESISTOR, THICK FILM, 130K, 100mW, 5%, 0603, 1608M
R10, R44, R45, R46, R47 | 5 | 22K_1608M | 22K_1608M | RESISTOR, THICK FILM, 22K, 100mW, 1%, 0603, 1608M
R11 | 1 | 102K_1608M | 102K_1608M | RESISTOR, THICK FILM, 102K, 100mW, 0.1%, 0603, 1608M
R12 | 1 | 9K53_1608M | 9K53_1608M | RESISTOR, THICK FILM, 9.53K, 100mW, 1%, 0603, 1608M
R13 | 1 | 39K_1608M | 39K_1608M
R14 | 1 | 1K2_1608M | 1K2_1608M | RESISTOR, THICK FILM, 1K2, 100mW, 1%, 0603, 1608M
R15 | 1 | 10K7_1608M | 10K7_1608M | RESISTOR, THICK FILM, 10.7K, 100mW, 1%, 0603, 1608M
R16 | 1 | 750K_1608M | 750K_1608M | RESISTOR, THICK FILM, 750K, 100mW, 1%, 0603, 1608M
R17 | 1 | 2R2_1608M | 2R2_1608M | RESISTOR, THICK FILM, 2.2R, 100mW, 5%, 0603, 1608M
R18 | 1 | 1R0_1608M | 1R0_1608M | RESISTOR, THICK FILM, 1R, 100mW, 5%, 0603, 1608M
R20, R21, R22 | 3 | 0R_1608M | 0R_1608M | RESISTOR, THICK FILM, 0R, 63mW, 0603, 1608M
R24 | 1 | R01_3216M | R01_3216M | RESISTOR, THICK FILM, 10mOhm, 1W, 1206, 3216M
R26 | 1 | 91K_1608M | 91K_1608M | RESISTOR, THICK FILM, 91K, 250mW, 1%, 0603, 1608M
R29, R35, R57 | 3 | 1K_QUAD_ARRAY_1608M | 1K_QUAD_ARRAY_1608M | RESISTOR, THICK FILM, 1K, 5%, 0603, 1608M, QUAD ARRAY
R3, R23, R36, R37, R38, R39, R55, R56, R61, R63, R70 | 11 | 10K0_1608M | 10K0_1608M | RESISTOR, THICK FILM, 10K, 125mW, 1%, 0603, 1608M
R30, R31, R67, R68 | 4 | 22R_1608M | 22R_1608M | RESISTOR, THICK FILM, 22R, 125mW, 1%, 0603, 1608M
R32, R40, R41, R42, R43, R50, R51 | 7 | 100R_1608M | 100R_1608M | RESISTOR, THICK FILM, 100R, 125mW, 1%, 0603, 1608M
R33, R34, R65, R66 | 4 | 4K7_1608M | 4K7_1608M | RESISTOR, THICK FILM, 100K, 125mW, 1%, 0603, 1608M
R4, R58, R59 | 3 | 2K40_1608M | 2K40_1608M | RESISTOR, THICK FILM, 2K4, 63mW, 1%, 0603, 1608M
R48 | 1 | 47R_QUAD_ARRAY_1608M | 47R_QUAD_ARRAY_1608M | RESISTOR, THICK FILM, 47R, 5%, 0603, 1608M, QUAD ARRAY
R49, R52, R53, R54, R62 | 5 | 10R_1608M | 10R_1608M | RESISTOR, THICK FILM, 10R, 125mW, 0603, 1608M
R5, R8, R9, R19, R25, R28 | 6 | 100K_1608M | 100K_1608M | RESISTOR, THICK FILM, 100K, 125mW, 1%, 0603, 1608M
R6 | 1 | 1M_1608M | 1M_1608M | RESISTOR, THICK FILM, 1M, 100mW, 1%, 0603, 1608M
R60 | 1 | 1K00_1608M | 1K00_1608M | RESISTOR, THICK FILM, 1K, 125mW, 1%, 0603, 1608M
R64 | 1 | 33K2_1608M | 33K2_1608M | RESISTOR, THICK FILM, 33K2, 63mW, 0603, 1608M
R69 | 1 | 16K9_1608M | 16K9_1608M | RESISTOR, THICK FILM, 16.9K, 100mW, 1%, 0603, 1608M
R7, R27 | 2 | 12K7_1608M | 12K7_1608M | RESISTOR, THICK FILM, 12.7K, 100mW, 75V, 1%, 0603, 1608M
SW1, SW2, SW3 | 3 | B3U-1000P_SPST-NO_SMD | B3U-1000P_SPST-NO_SMD | B3U-1000P - Tactile Switch, SPST-NO, Non Illuminated, 12 V, 50 mA, 1.5 N, Solder, B3U Series
TEST1 | 1 | CLIP_HOOK_BROWN | CLIP_HOOK_BROWN | PCB Probe Hook, BROWN, Through Hole
TEST2 | 1 | CLIP_HOOK_YELLOW | CLIP_HOOK_YELLOW | PCB Probe Hook, YELLOW, Through Hole
TEST3 | 1 | CLIP_HOOK_RED | CLIP_HOOK_RED | PCB Probe Hook, RED, Through Hole
TEST4 | 1 | CLIP_HOOK_ORANGE | CLIP_HOOK_ORANGE | PCB Probe Hook, ORANGE, Through Hole
TEST5 | 1 | CLIP_HOOK_BLACK | CLIP_HOOK_BLACK | PCB Probe Hook, BLACK, Through Hole
TEST6, TEST8 | 2 | PROBE_PAD | PROBE_PAD | Test pad, PCB circular, pad
TH1, TH2 | 2 | NTC_10K_1608M | NTC_10K_1608M | THERMISTOR, NTC, 10K, 2%, NTC, 1608M, 0603
U1, U3 | 2 | ISL85410FRZ | ISL85410FRZ | ISL85410FRZ, Step-down SMPS, 3V-40V supply, adjustable output, 1A drive, DFN12
U10, U11 | 2 | ULN2003A | ULN2003A | Darlington Transistor Array, Octal, 50V, 500mA, Logic-level, SOIC18
U12 | 1 | ADUM5412 | ADUM5412 | Digital Isolator & Isolated Regulator, 4-ch, 2 input/2 output, 150mW output, 150Mb/s, 3.75kV isolation, 1.7-5.5V supply, 3.15-5.25V output, SSOP 24
U2 | 1 | LM5116 | LM5116 | Step-down DC-DC controller, 15-85V IN, 1.25-80V OUT, TSSOP-20
U4 | 1 | STM32F429VET6 | STM32F429VET6 | ST STM32F429VET6, ARM Cortex-M4, 32bit, 180 MHz, 512 KB Flash, 256 KB SRAM, 100 Pins
U5 | 1 | ADUM3160 | ADUM3160 | Digital Isolator, USB LS FS, 4-ch bidirectional, 12Mb/s, SOIC 16
U6, U7, U8, U9 | 4 | ACS711KEXLT_15AB | ACS711KEXLT_15AB | Current Sensor, 15.5A, 100kHz, <100V isolation, 1 Channel, Hall Effect, Bidirectional, 12-WFQFN
X1 | 1 | CSTCE8M00G55Z | CSTCE8M00G55Z | Murata Ceramic Resonator, 8MHz Shear 33pF, 3-Pin SMT
X2 | 1 | SWD_SMT_SOCKET | SWD_SMT_SOCKET | Cortex-M Debug Connector, SWD, JTAG (Header 1.27mm pitch 10-way 2x5)
X3 | 1 | ABS06-107-32.768KHZ | ABS06-107-32.768KHZ | RESONATOR, SMD, 32.768KHz, 175ppm, 4pF

Generated: 1/05/2018 12:11:17 AM
Script: F:\Projects\ECAD\Applidyne\scripts\BOM\bom\bom_html_by_value.py
Version: Eeschema (5.0.0-rc2-dev-296-g4594fedc2)

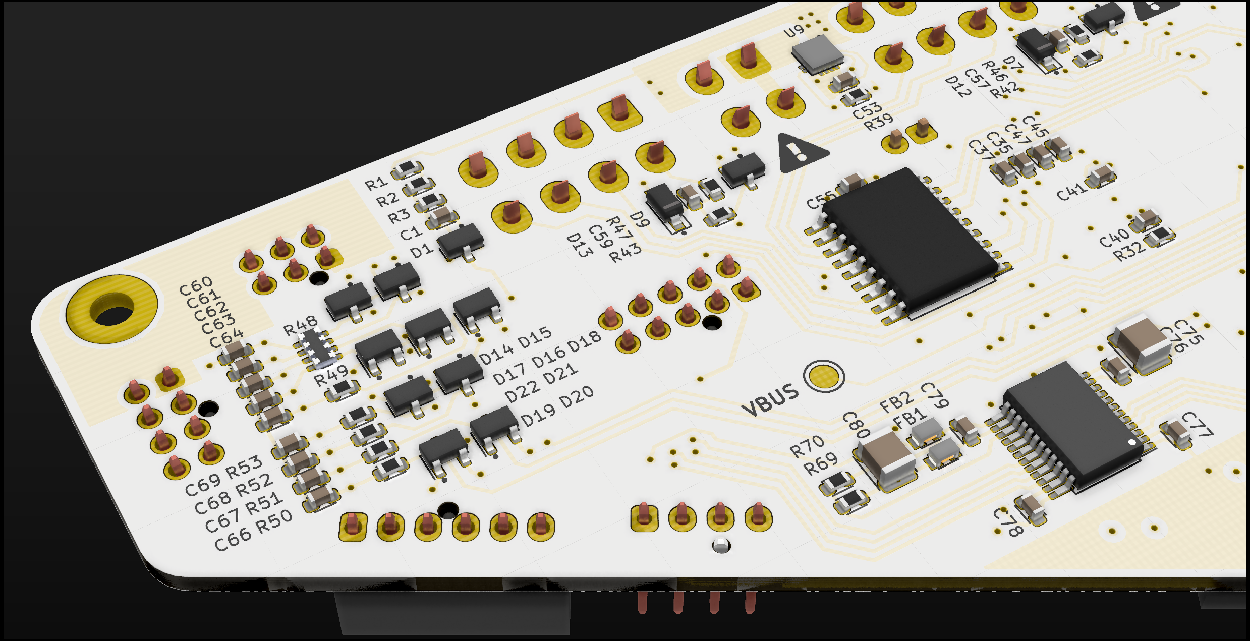
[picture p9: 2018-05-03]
electronics/imgs/expansion_detail_bottom.png

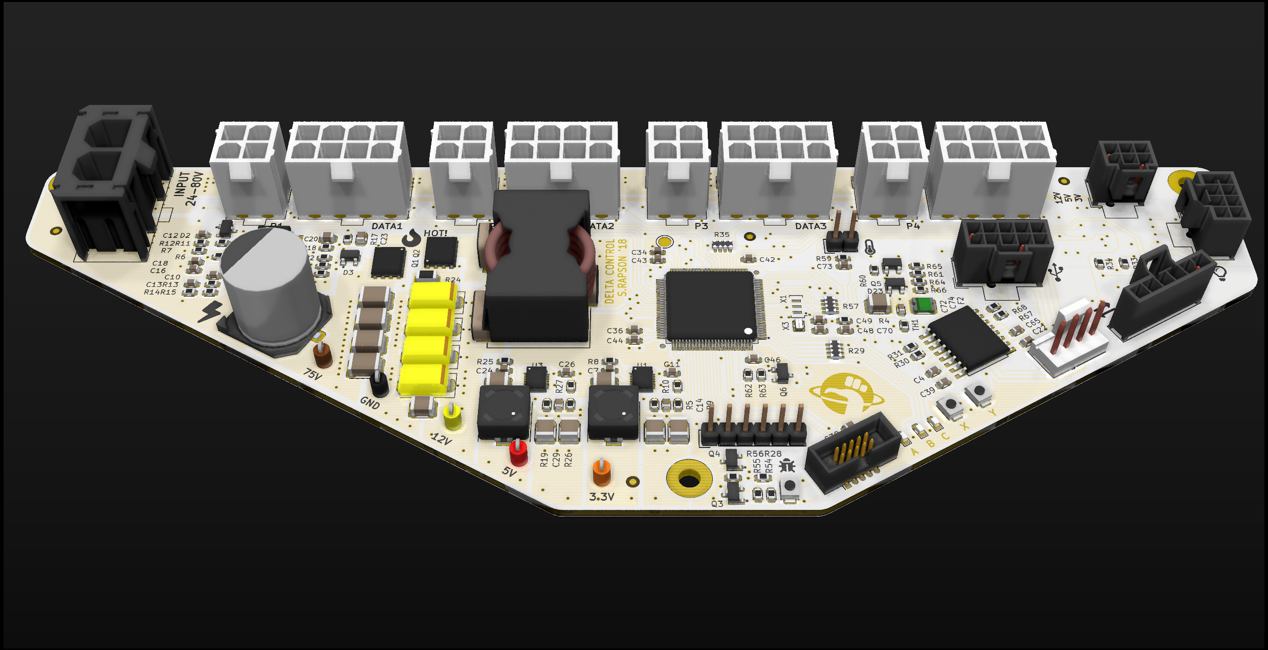
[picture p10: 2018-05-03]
electronics/imgs/overview_top.png

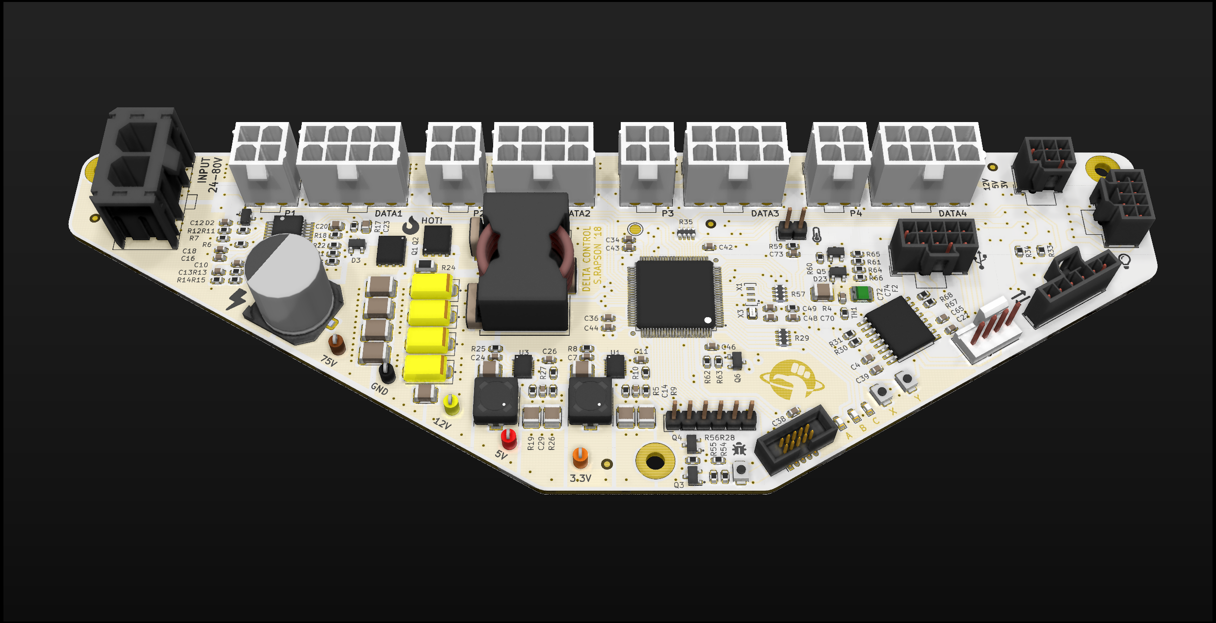
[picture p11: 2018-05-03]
electronics/imgs/overview_front_edge.png

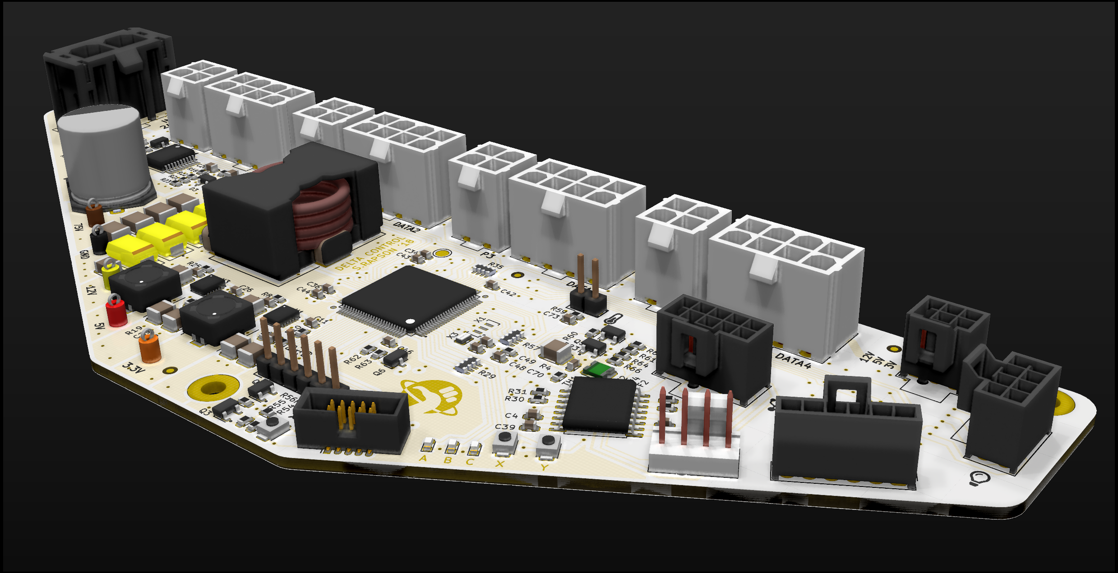
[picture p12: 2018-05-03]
electronics/imgs/overview_side_edge.png

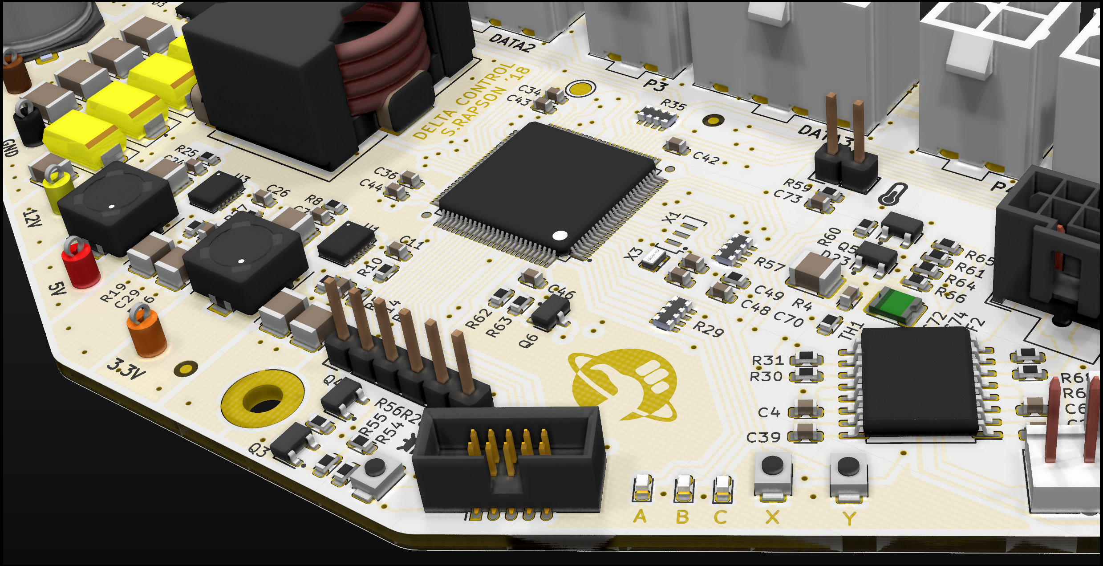
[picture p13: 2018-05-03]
electronics/imgs/logic_area.png

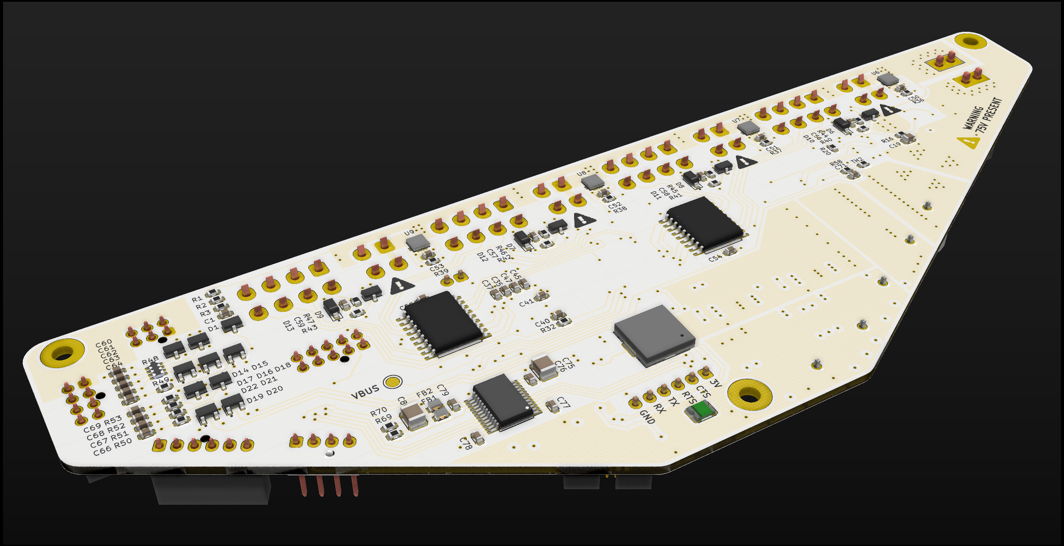
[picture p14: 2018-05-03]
electronics/imgs/overview_bottom.png

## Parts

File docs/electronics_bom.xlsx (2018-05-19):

Category | Part | Link | Price ea, AUD | Qty | MOQ | Total | Purchased
Input Power | IEC320 Connector | https://www.jaycar.com.au/iec-fuse-chassis-male-power-plug-with-switch/p/PP4003 | $7 | 1 | 1 | $7 | Y
Input Power | M205 Quick Blow Fuse 4A | https://www.jaycar.com.au/4a-m205-quick-blow-fuse/p/SF2164 | 1.1 | 1 | 1 | $1.1 | Y
Input Power | Spade Terminals |  | 0.56 | 2 | 10 | $1.12 | Y
Input Power | Mains 3-wire 2.54m^2 |  | 0 | 1 | 1 | $0 | N
Input Power | MiniFit 4x2 | https://au.rs-online.com/web/p/pcb-connector-housings/4841782/ | 0.63 | 1 | 5 | $0.63 | Y
Input Power | Teknic IPC-3 PSU | https://www.teknic.com/products/servo-motor-dc-power-supply/#ipc-3-info | 260 | 1 |  | $260 | Y
Input Power | Molex SABRE 2x1 | https://au.rs-online.com/web/p/pcb-connector-housings/3639875/ | 1.76 | 2 | 5 | $3.52 | Y
Input Power | Molex SABRE crimps | https://au.rs-online.com/web/p/pcb-connector-contacts/6702437/?sra=pstk | 0.102 |  | 100 | $0 | Y
Input Power | 14AWG BLACK |  |  | 1 |  | $0
Input Power | 14AWG RED |  |  | 1 |  | $0
Control | Main Control PCB Assembled | Custom build | 310 | 3 |  | $930 | Y | See control PCB BOM for estimated pricing
Motor Power | Molex MiniFit 2x2 | https://au.rs-online.com/web/p/pcb-connector-housings/6704575 | 1.087 | 8 | 10 | $8.696 | Y
Motor Power | 16AWG BLACK
Motor Power | 16AWG RED
Motor Control | Molex Minifit 4x2 | https://au.rs-online.com/web/p/pcb-connector-housings/8428197/?sra=pstk | 0.465 | 8 | 10 | $3.72 | Y
Motor Control | 20AWG
Other | Molex MiniFit Crimps | https://au.rs-online.com/web/p/pcb-connector-contacts/2155887/?sra=pstk | 0.232 |  | 100 | $0 | Y

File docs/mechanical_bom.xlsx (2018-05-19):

Category | Part | Detail | Link | Price ea, AUD | Qty per | Qty Units | Total | Purchased
Linkages and Effector | Bicep | Machined 6061-T6 |  | $62.00 | 1 | 3 | $186.00 | Y
 | Bicep Elbow | Machined 6061-T6 |  | $31.00 | 1 | 3 | $93.00 | Y
 | Bicep->motor bolt | M3x8 cap head |  |  | 1 | 3 | $0.00 | Y
 | Elbow Shoulder bolts | 4x4mm shoulder, M3x4 thread, hex |  | $0.90 | 2 | 3 | $5.40 | Y
 | Elbow-side bearings | 4x9x4 bearing |  | $1.25 | 2 | 3 | $7.50 | Y
 | End effector | 3D Printed SLA |  |  | 1 | 1 | $0.00 | Y
 | Effector cover plate | 2.0mm carbon CNC |  | $3.20 | 1 | 1 | $3.20 | Y
 | Effector plate nutserts | M3 steel nutsert |  |  | 3 | 1 | $0.00 | Y
 | Effector plate bolts | M3x8 button head |  |  | 3 | 1 | $0.00 | Y
 | Effector Shoulder Bolts | 4x4mm shoulder, M3x4 thread, hex |  | $0.90 | 2 | 3 | $5.40 | Y
 | Effector-side bearings | 4x9x4 bearing |  | $1.25 | 2 | 3 | $7.50 | Y
 | Carbon forearms | 8x6x500 3K tube |  | $11.00 | 2 | 3 | $66.00 | Y
 | Clevis inserts | 3D Printed SLA |  |  | 4 | 3 | $0.00 | Y
 | Clevis shoulderbolts | 4x8mm shoulder, M3x4 thread, hex |  | $0.90 | 4 | 3 | $10.80 | Y
 | Clevis shoulderbolt nut | M3 Nyloc |  | $0.10 | 4 | 3 | $1.20 | Y
 | Clevis-side bearings | 4x9x4 bearing |  | $1.25 | 4 | 3 | $15.00 | Y
 | Bearing joint | 3D Printed SLA |  |  | 4 | 3 | $0.00 | Y
Motor Mounts | Motor Angle Mount | Machined 6061-T6 |  | $17.00 | 1 | 3 | $51.00 | Y
 | Base-Angle Bolts | M5x12 Countersunk |  |  | 4 | 3 | $0.00 | Y
 | Motor-Angle bolts | M5x10 Cap Screw |  |  | 4 | 3 | $0.00 | Y
Housing | Top Plate | Machined 6061-T6 |  | $102.00 | 1 | 1 | $102.00 | Y
 | Bottom Plate | Machined 6061-T6 |  | $102.00 | 1 | 1 | $102.00 | Y
 | Bottom Plate Cover | 2.0mm carbon CNC |  |  | 1 | 1 | $0.00 | Y
 | Cover bolts | M3x6 |  |  | 5 | 1 | $0.00 | Y
 | Cover nutserts | M3 steel nutsert |  |  |  |  | $0.00 | Y
 | Plate Pillars | Machined 6061-T6 |  | $15.50 | 6 | 1 | $93.00 | Y
 | Alu Plate Fasteners | M5x12 to M5x16 Countersunk |  |  | 6 | 2 | $0.00 | Y
 | Carbon Cover Blank | 2.0mm carbon CNC |  | $8.00 | 1 | 4 | $32.00 | Y
 | Carbon Cover Exhaust | 2.0mm carbon CNC |  | $8.00 | 1 | 1 | $8.00 | Y
 | Carbon Cover Electronics | 2.0mm carbon CNC |  | $8.00 | 1 | 1 | $8.00 | Y
 | Carbon Cover Fasteners | M3x8 button head |  |  | 4 | 6 | $0.00 | Y
PSU Mount | PSU bracket | Machined 6061-T6 |  | $21.00 | 1 | 1 | $21.00 | Y
 | Plate-Bracket bolts | M5x12 Countersunk |  |  | 4 | 1 | $0.00 | Y
 | Bracket-PSU bolts | M3x8 |  |  | 3 | 1 | $0.00 | Y

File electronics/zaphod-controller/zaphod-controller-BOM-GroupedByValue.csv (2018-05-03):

Ref | Qty | Value | Description | Manf | Manf# | Installed | Footprint
C1, C4, C7, C16, C22, C24, C37, C38, C39, C40, C41, C42, C43, C44, C46, C47, C50, C51, C52, C53, C54, C55, C65, C70, C71, C73, C74, C76, C77, C78, C79 | 31 | 100n_X7R_1608M | CAP, MLCC, X7R, 100NF, 50V, 0603 | KEMET | C0603C104K5RACAUTO |  | CAPC1608X90N
C10 | 1 | 15p_X7R_1608M | CAP, MLCC, C0G/NP0, 15PF, 50V, 5%, 0603, 1608M | TDK | C1608C0G1H150J080AA |  | CAPC1608X90N
C11, C12, C26, C34, C35, C36, C45 | 7 | 1u_X7R_1608M | CAP, MLCC, X7R, 1UF, 50V, 0603 | muRata | GRM188R61H105KAALD | b | CAPC1608X90N
C13 | 1 | 1n5_X7R_1608M | CAP, MLCC, X7R, 1500PF, 50V, 10%, 0603, 1608M | muRata | GRM188R71H152KA01D |  | CAPC1608X90N
C14, C29, C48, C49 | 4 | 22p_X7R_1608M | CAP, MLCC, X7R, 22PF, 50V, 0603 | MULTICOMP | MC0603N220K500CT |  | CAPC1608X90N
C15, C17, C31, C32, C33, C72 | 6 | 22u_X7R_3225M | CAP, MLCC, X7R, 22UF, 25V, 10%, 1210, 3225M | muRata | C1210C226K3RACTU | b | CAPC3225X170N
C18 | 1 | 330p_X7R_1608M | CAP, MLCC, X7R, 330PF, 50V, 0603, 1608M | AVX | 06035A331JAT2A |  | CAPC1608X90N
C19, C20, C23 | 3 | 1u_X7R_2012M | CAP, MLCC, X7R, 1UF, 16V, 0805, 2012M | muRata | GRM21BR71C105KA01L |  | CAPC2012X110N
C2 | 1 | 47u_ELEC_100V_1350X1350M | CAP, ALU ELEC, 47UF, 100V, 320mOhm, AEC-Q200, 5000 hour, SMD | PANASONIC | EEV-FK2A470Q | b | CAPAE1350X1350D1490DD450L470N
C25, C27, C28, C30 | 4 | 47u_TANT_7343M | CAP, TANT, 47UF, 16V, 7343-31 | KEMET | T520D476M016ATE035 | b | CAPPM7343X310N
C3, C21, C75, C80 | 4 | 10u_X7R_3225M | CAP, MLCC, X7R, 10UF, 25V, 1210 3225M | WURTH ELEKTRONIK | 885012209028 |  | CAPC3225X170N
C5, C6, C8, C9 | 4 | 2u2_X7R_4532M | CAP, MLCC, X7R, 2.2UF, 100V, 1812, 4532M | TDK | C4532X7R2A225M230KA | b | CAPC4532X180N
C56, C57, C58, C59 | 4 | 10n_X7R_1608M | CAP, MLCC, X7R, 10NF, 25V, 0603 | AVX | 06033C103KAT2A |  | CAPC1608X90N
C60, C61, C62, C63, C64, C66, C67, C68, C69 | 9 | 1n_X7R_1608M | CAP, MLCC, X7R, 1NF, 100V, 0603 | AVX | 06031C102KAT2A |  | CAPC1608X90N
D1, D6, D7, D8, D9, D14, D15, D16, D17, D18, D19, D20, D21, D22, D23 | 15 | BAV99 | DIODE DUAL, 100V, 215mA, 4ns, SOT23 | NXP | BAV99 | b | SOT95P240X110-3L16N
D10, D11, D12, D13 | 4 | 3V3 | DIODE, Zener 3V3, 500mW, SOD123 | VISAY SEMICONDUCTOR | MMSZ5226 |  | SOD3715X145N
D2, D3 | 2 | 200V_350mW_SOT23 | CMPD2003C DIODE DUAL, Common Cathode, 200V, 200mA, 4A peak, 350mW, SOT23-3 | Central Semiconductor | CMPD2003C-TR | b | SOT95P240X110-3L16N
D24 | 1 | LED_RED_1608M | DIALIGHT ChipLED Red, 0603, 1608M | DIALIGHT | 5988010107F |  | LEDC1608X80L40N
D4 | 1 | LED_YELLOW_1608M | DIALIGHT ChipLED Yellow, 0603, 1608M | DIALIGHT | 5988040107F |  | LEDC1608X80L40N
D5 | 1 | LED_GREEN_1608M | DIALIGHT ChipLED Green, 0603, 1608M | DIALIGHT | 5988070107F |  | LEDC1608X80L40N
F1, F2 | 2 | 0.5A_1210L_PTC | FUSE, RESETTABLE, PTC, 13.2VDC, 500mA, SMD, 1210L050 | LittelFuse | 1210L050YR | b | FUSC3225X85L50N
FB1, FB2 | 2 | 1K_1608M | FERRITE BEAD, 1Kohm @ 100MHz, 0.6Ohm, 100mA, 0603, 1608M | muRata | BLM18TG102TN1D | b | INDC1608X95N
L1, L2 | 2 | 22u_MCSDRH73B | INDUCTOR, 22UH, 1.83A, Shielded, 0.13ohm | MULTICOMP | MCSDRH73B-220MHF |  | INDM7373X355L170X207N
L3 | 1 | 10u2_PA2050 | INDUCTOR, 10.2UH, 12.5A, 10%, 0.0058ohm | PULSE ELECTRONICS | PA2050.103NL | b | PULSE_PA2050
LS1 | 1 | PKMCS0909E4000-R1 | Murata Buzzer, passive, piezo transducer, 12V, 9x9x1.9mm, SMD, top firing | muRata | PKMCS0909E4000-R1 | b | MURATA_PKMCS0909E4000
P1 | 1 | MOLEX_43160-0102 | AS7.5mm pitch, Vertical, PTH, 2 contacts | MOLEX | 043160-0102 | b | Molex_Sabre_43160-0102_VERT
P11, P12, P13, P14 | 4 | MOLEX_MINIFIT_JR_2x4_WAY | CONNECTOR, SOCKET, 8POS, 2ROW, MINI-FIT JR, 5566 series, 4.2MM pitch, PTH | MOLEX | 172447-0208 | b | Molex_Mini-Fit_Jr_5566-08A_2x04_P4.20mm_Vertical
P15 | 1 | MOLEX_NANOFIT_2x4_WAY | CONNECTOR, SOCKET, 8POS, 2ROW, Nano-fit, 105310 series, 2.5MM pitch, PTH | MOLEX | 105310-1108 | b | Molex_Nano-Fit_105310-xx08_2x04_VERT
P16 | 1 | MOLEX_NANOFIT_1x6_WAY | PCB Socket, 2.5mm pitch, 105309 series, Vertical, PTH, 6-WAY, 1-ROW | MOLEX | 105313-1106 | b | Molex_Nano-Fit_105309-xx06_1x06_VERT
P17 | 1 | MOLEX_NANOFIT_2x3_WAY | PCB Socket, 2.5mm pitch, 105310 series, Vertical, PTH, 6-WAY, 2-ROW | MOLEX | 105310-1204 | b | Molex_Nano-Fit_105310-xx06_2x03_VERT
P18 | 1 | CONN_01X02 | Pin Header, 2.54mm, Vertical, PTH, 2 Way, 1 Row, 01x02 | WURTH | 61300211121 |  | 61300211121
P19 | 1 | MOLEX_KK2.54_1x4_WAY_FAN | CONNECTOR, SOCKET, 4POS, 1ROW, KK 2.54, 2.54mm pitch, PWM fan header, PTH | MOLEX | 47053-1000 | b | MOLEX_47053-1000
P2, P3, P4, P5 | 4 | MOLEX_MINIFIT_JR_2x2_WAY | CONNECTOR, SOCKET, 4POS, 2ROW, MINI-FIT JR, 5566 series, 4.2MM pitch, Vertical PTH | MOLEX | 172447-0204 | b | Molex_Mini-Fit_Jr_5566-04A_2x02_P4.20mm_Vertical
P20 | 1 | CONN_01X06 | Pin Header, 2.54mm, Vertical, PTH, 6 Way, 1 Row, 01x06 | WURTH | 61300611121 |  | 61300611121
P21 | 1 | MOLEX_NANOFIT_2x5_WAY | CONNECTOR, SOCKET, 10POS, 2ROW, Nano-fit, 105310 series, 2.5MM pitch, PTH | MOLEX | 105310-1110 | b | Molex_Nano-Fit_105310-xx10_2x05_VERT
Q1, Q2 | 2 | Si7852DP | MOSFET N-CH, 80V, 12.5A, 16.5mOhm, SOT-23 | Vishay | SI7852DP-T1-GE3 | b | SON127P490X575X90-9T313X381N
Q3, Q6 | 2 | 2N7002P | MOSFET N-CH 60V 0.36A SOT-23 | Fairchild | 2N7002,215 | b | SOT95P240X110-3L16N
Q4 | 1 | NTR1P02T1G | MOSFET, P-CH, 1A, -20V, 0.148ohm, -10V, -1.9V | On Semi | NTR1P02T1G | b | SOT95P240X110-3L16N
Q5 | 1 | BC847B | Transistor, NPN, 45V, 100MHz, 250mW, 100mA, 250mW, SOT-23 | Multicomp | BC847B | b | SOT95P240X110-3L16N
R1, R2 | 2 | 130K_1608M | RESISTOR, THICK FILM, 130K, 100mW, 5%, 0603, 1608M | PANASONIC | ERJ3GEYJ134V |  | RESC1608X50N
R10, R44, R45, R46, R47 | 5 | 22K_1608M | RESISTOR, THICK FILM, 22K, 100mW, 1%, 0603, 1608M | MULTICOMP | MCMR06X2202FTL |  | RESC1608X50N
R11 | 1 | 102K_1608M | RESISTOR, THICK FILM, 102K, 100mW, 0.1%, 0603, 1608M | MULTICOMP | MCWF06R1023BTL |  | RESC1608X50N
R12 | 1 | 9K53_1608M | RESISTOR, THICK FILM, 9.53K, 100mW, 1%, 0603, 1608M | VISHAY | CRCW06039K53FKEA |  | RESC1608X50N
R13 | 1 | 39K_1608M | No description | PANASONIC | MCMR06X2202FTL |  | RESC1608X50N
R14 | 1 | 1K2_1608M | RESISTOR, THICK FILM, 1K2, 100mW, 1%, 0603, 1608M | VISHAY | CRCW06031K20FKEA |  | RESC1608X50N
R15 | 1 | 10K7_1608M | RESISTOR, THICK FILM, 10.7K, 100mW, 1%, 0603, 1608M | PANASONIC | ERJ3EKF1072V |  | RESC1608X50N
R16 | 1 | 750K_1608M | RESISTOR, THICK FILM, 750K, 100mW, 1%, 0603, 1608M | MULTICOMP | MCSR06X7503FTL |  | RESC1608X50N
R17 | 1 | 2R2_1608M | RESISTOR, THICK FILM, 2.2R, 100mW, 5%, 0603, 1608M | PANASONIC | ERJ-S03J2R2V |  | RESC1608X50N
R18 | 1 | 1R0_1608M | RESISTOR, THICK FILM, 1R, 100mW, 5%, 0603, 1608M | MULTICOMP | MCMR06X1R0JTL |  | RESC1608X50N
R20, R21, R22 | 3 | 0R_1608M | RESISTOR, THICK FILM, 0R, 63mW, 0603, 1608M | MULTICOMP | MC0063W06030R |  | RESC1608X50N
R24 | 1 | R01_3216M | RESISTOR, THICK FILM, 10mOhm, 1W, 1206, 3216M | Vishay | WSLP1206R0100FEA |  | RESC3216X140N
R26 | 1 | 91K_1608M | RESISTOR, THICK FILM, 91K, 250mW, 1%, 0603, 1608M | PANASONIC | ERJPA3F9102V |  | RESC1608X50N
R29, R35, R57 | 3 | 1K_QUAD_ARRAY_1608M | RESISTOR, THICK FILM, 1K, 5%, 0603, 1608M, QUAD ARRAY | BOURNS | CAY16-102J4LF | b | R_Array_Concave_4x1608M
R3, R23, R36, R37, R38, R39, R55, R56, R61, R63, R70 | 11 | 10K0_1608M | RESISTOR, THICK FILM, 10K, 125mW, 1%, 0603, 1608M | TE CONNECTIVITY | CRGH0603F10K |  | RESC1608X50N
R30, R31, R67, R68 | 4 | 22R_1608M | RESISTOR, THICK FILM, 22R, 125mW, 1%, 0603, 1608M | MULTICOMP | MC0063W060314R22 |  | RESC1608X50N
R32, R40, R41, R42, R43, R50, R51 | 7 | 100R_1608M | RESISTOR, THICK FILM, 100R, 125mW, 1%, 0603, 1608M | MULTICOMP | MC0063W06035100R |  | RESC1608X50N
R33, R34, R65, R66 | 4 | 4K7_1608M | RESISTOR, THICK FILM, 100K, 125mW, 1%, 0603, 1608M | MULTICOMP | MC0063W060354K7 |  | RESC1608X50N
R4, R58, R59 | 3 | 2K40_1608M | RESISTOR, THICK FILM, 2K4, 63mW, 1%, 0603, 1608M | MULTICOMP | MC0063W060312K4 |  | RESC1608X50N
R48 | 1 | 47R_QUAD_ARRAY_1608M | RESISTOR, THICK FILM, 47R, 5%, 0603, 1608M, QUAD ARRAY | PANASONIC | EXBV8V470JV | b | R_Array_Concave_4x1608M
R49, R52, R53, R54, R62 | 5 | 10R_1608M | RESISTOR, THICK FILM, 10R, 125mW, 0603, 1608M | MULTICOMP | MCHP03W8F100JT5E |  | RESC1608X50N
R5, R8, R9, R19, R25, R28 | 6 | 100K_1608M | RESISTOR, THICK FILM, 100K, 125mW, 1%, 0603, 1608M | MULTICOMP | MC0063W06035100K |  | RESC1608X50N
R6 | 1 | 1M_1608M | RESISTOR, THICK FILM, 1M, 100mW, 1%, 0603, 1608M | VISHAY DRALORIC | CRCW06031M00FKEA |  | RESC1608X50N
R60 | 1 | 1K00_1608M | RESISTOR, THICK FILM, 1K, 125mW, 1%, 0603, 1608M | MULTICOMP | MCHP03W8F1001T5E |  | RESC1608X50N
R64 | 1 | 33K2_1608M | RESISTOR, THICK FILM, 33K2, 63mW, 0603, 1608M | PANASONIC | ERJPA3F3322V |  | RESC1608X50N
R69 | 1 | 16K9_1608M | RESISTOR, THICK FILM, 16.9K, 100mW, 1%, 0603, 1608M | PANASONIC | ERJ3EKF1692V |  | RESC1608X50N
R7, R27 | 2 | 12K7_1608M | RESISTOR, THICK FILM, 12.7K, 100mW, 75V, 1%, 0603, 1608M | PANASONIC | ERJ3EKF1272V |  | RESC1608X50N
SW1, SW2, SW3 | 3 | B3U-1000P_SPST-NO_SMD | B3U-1000P - Tactile Switch, SPST-NO, Non Illuminated, 12 V, 50 mA, 1.5 N, Solder, B3U Series | OMRON | B3U-1000P | b | B3U-1000P
TEST1 | 1 | CLIP_HOOK_BROWN | PCB Probe Hook, BROWN, Through Hole | KEYSTONE | 5115 |  | KEYSTONE_5115
TEST2 | 1 | CLIP_HOOK_YELLOW | PCB Probe Hook, YELLOW, Through Hole | KEYSTONE | 5004 |  | KEYSTONE_5004
TEST3 | 1 | CLIP_HOOK_RED | PCB Probe Hook, RED, Through Hole | KEYSTONE | 5000 |  | KEYSTONE_5000
TEST4 | 1 | CLIP_HOOK_ORANGE | PCB Probe Hook, ORANGE, Through Hole | KEYSTONE | 5003 |  | KEYSTONE_5003
TEST5 | 1 | CLIP_HOOK_BLACK | PCB Probe Hook, BLACK, Through Hole | KEYSTONE | 5001 |  | KEYSTONE_5001
TEST6, TEST8 | 2 | PROBE_PAD | Test pad, PCB circular, pad | N/A | N/A |  | TP200
TH1, TH2 | 2 | NTC_10K_1608M | THERMISTOR, NTC, 10K, 2%, NTC, 1608M, 0603 | MURATA | NCP18XH103J03RB | b | RESC1608X50N
U1, U3 | 2 | ISL85410FRZ | ISL85410FRZ, Step-down SMPS, 3V-40V supply, adjustable output, 1A drive, DFN12 | RENESAS/INTERSIL | ISL85410FRZ | b | QFN50P400X300X100-13T170X330N
U10, U11 | 2 | ULN2003A | Darlington Transistor Array, Octal, 50V, 500mA, Logic-level, SOIC18 | TI | ULN2803ADW | b | SOIC127P1030X265-18L87N
U12 | 1 | ADUM5412 | Digital Isolator & Isolated Regulator, 4-ch, 2 input/2 output, 150mW output, 150Mb/s, 3.75kV isolation, 1.7-5.5V supply, 3.15-5.25V output, SSOP 24 | Analog Devices | ADUM5412BRSZ | b | SOP65P780X200-24L40N
U2 | 1 | LM5116 | Step-down DC-DC controller, 15-85V IN, 1.25-80V OUT, TSSOP-20 | TEXAS INSTRUMENTS | LM5116MHX | b | SOP21P65_720X780X200L75X30N
U4 | 1 | STM32F429VET6 | ST STM32F429VET6, ARM Cortex-M4, 32bit, 180 MHz, 512 KB Flash, 256 KB SRAM, 100 Pins | ST MICROELECTRONICS | STM32F429VET6 | b | QFP50P1600X1600X160-100L25N
U5 | 1 | ADUM3160 | Digital Isolator, USB LS FS, 4-ch bidirectional, 12Mb/s, SOIC 16 | Analog Devices | ADUM3160BRWZ | b | SOIC127P1032X265-16L87N
U6, U7, U8, U9 | 4 | ACS711KEXLT_15AB | Current Sensor, 15.5A, 100kHz, <100V isolation, 1 Channel, Hall Effect, Bidirectional, 12-WFQFN | Allegro MicroSystems | ACS711KEXLT-15AB-T |  | ACS-EX-12
X1 | 1 | CSTCE8M00G55Z | Murata Ceramic Resonator, 8MHz Shear 33pF, 3-Pin SMT | Murata | CSTCE8M00G55Z-R0 | b | OSCSC-CSCTE-CERALOCK
X2 | 1 | SWD_SMT_SOCKET | Cortex-M Debug Connector, SWD, JTAG (Header 1.27mm pitch 10-way 2x5) | CNC TECH | 3220-10-0300-00 | b | CNCTECH_3220-10-0300-00
X3 | 1 | ABS06-107-32.768KHZ | RESONATOR, SMD, 32.768KHz, 175ppm, 4pF | ABRACON | ABS06-107-32.768KHZ-T | b | XTALDFN200X120X60-2N

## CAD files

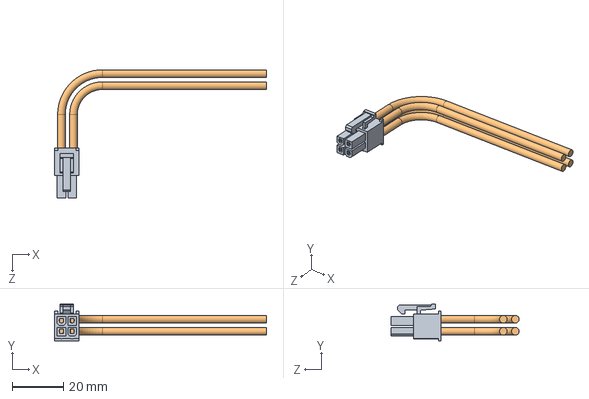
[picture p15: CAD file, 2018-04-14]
mechanical/design/cots-modified/4_pin_motor_loom/clearpath_power_loom.SLDASM
82.7 x 14.4 x 50.1 mm
microfit_2x2_loom

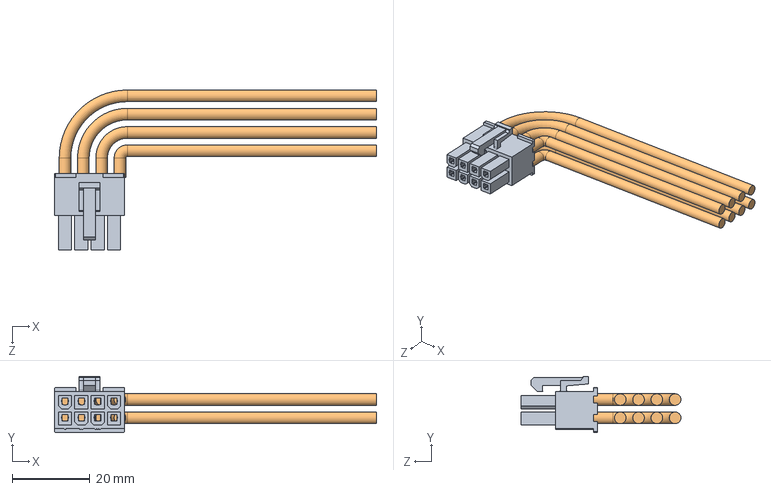
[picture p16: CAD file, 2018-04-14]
mechanical/design/cots-modified/8_pin_motor_loom/clearpath_data_loom.SLDASM
82.7 x 14.4 x 41.1 mm
microfit_4x2_loom

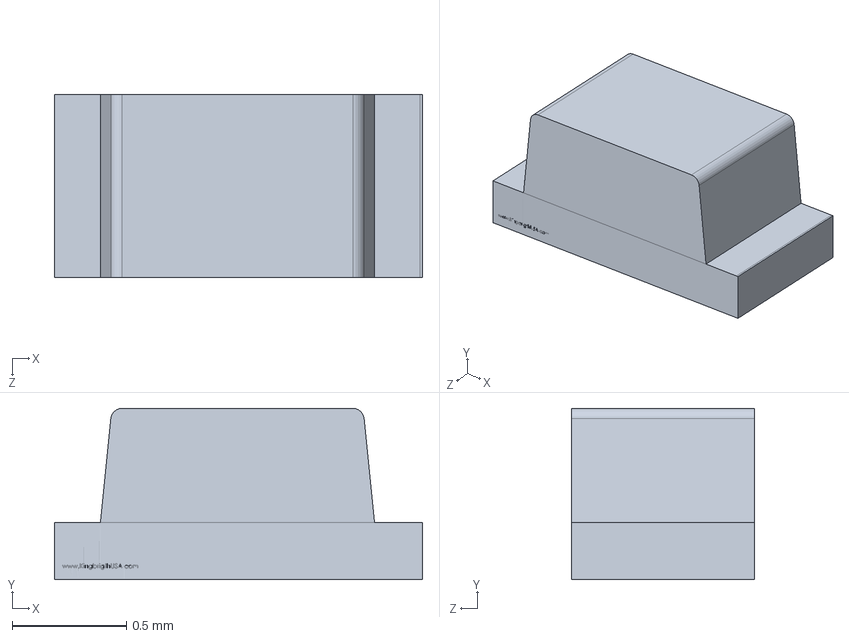
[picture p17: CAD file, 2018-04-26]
mechanical/design/cots-modified/pcb/LEDC1608X80L40.sldasm
1.61 x 0.75 x 0.8 mm

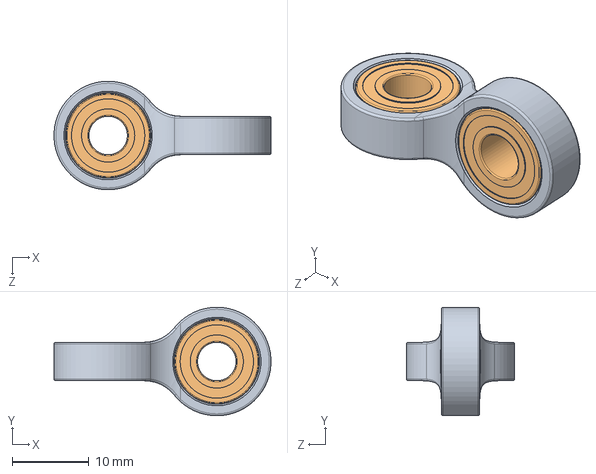
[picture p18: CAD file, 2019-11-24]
mechanical/design/linkage_uni_bearing/bearing_link_assembly.SLDASM
28.2 x 14.1 x 14.1 mm
bearing_link
SB685ZZ x 2

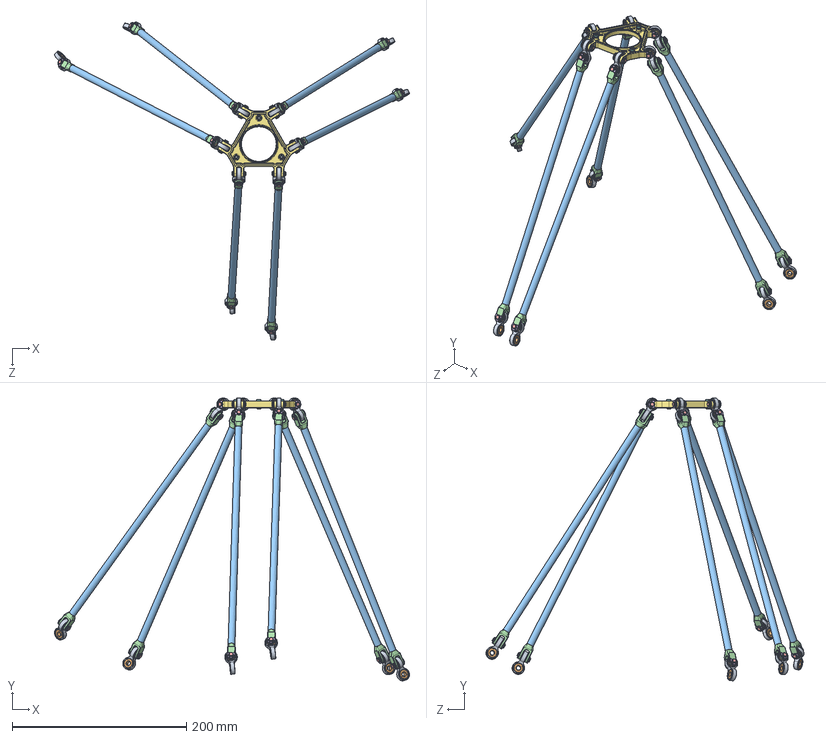
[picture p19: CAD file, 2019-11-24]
mechanical/design/linkage_uni_bushing/arm_mech_assembly_bushed.SLDASM
408.0 x 324.9 x 365.6 mm
bearing_link x 12
SB685ZZ x 24
8x6 Carbon Tube x 6
clevis x 12
_CDG5-12D x 18
_No.4_1 x 36
effector_planar
nutsert_M3 x 3
socket button head cap screw_am x 3

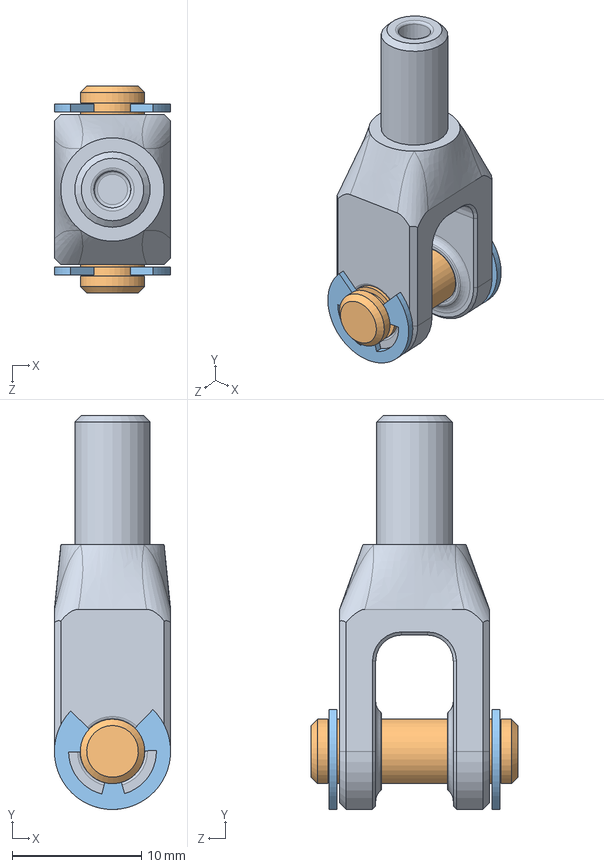
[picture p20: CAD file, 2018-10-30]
mechanical/design/linkage_uni_bearing/clevis_assembly.SLDASM
9.00 x 30.5 x 16.0 mm
clevis
_CDG5-12D
_No.4_1 x 2

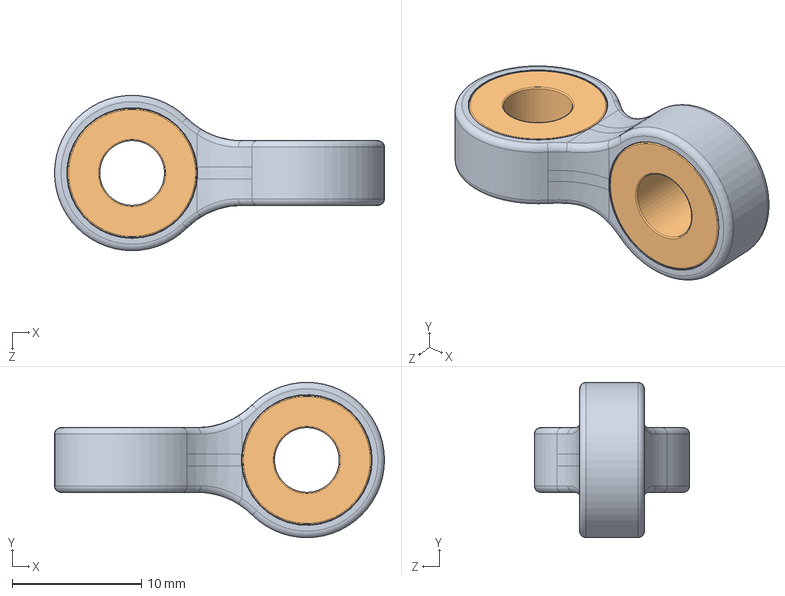
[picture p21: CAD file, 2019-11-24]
mechanical/design/linkage_uni_bushing/bushing_link_assembly.SLDASM
25.5 x 12.0 x 12.0 mm
bushing_link
GFM-0506-05 x 2

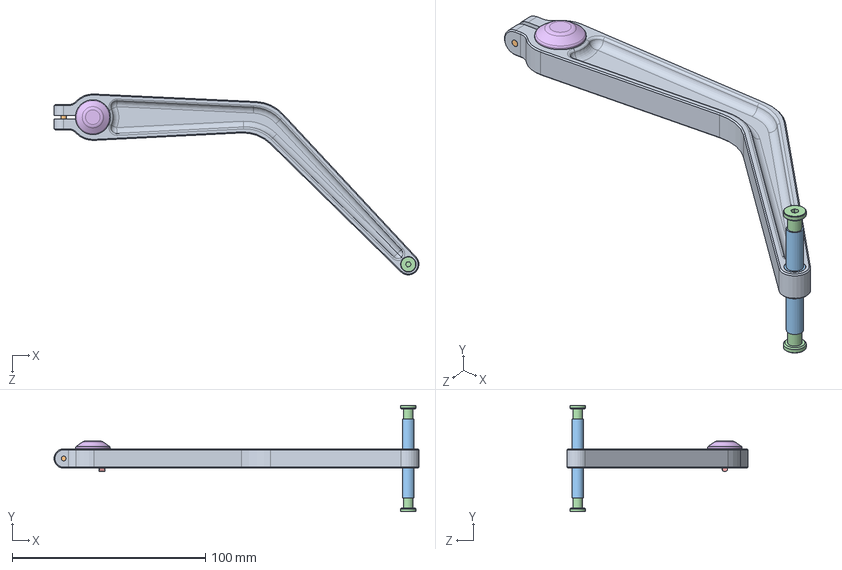
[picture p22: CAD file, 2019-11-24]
mechanical/design/bicep_assembly.SLDASM
188.7 x 55.0 x 93.6 mm
bicep2
socket head cap screw_am
bicep_elbow
BGSP5-8-L5 x 2
KES3_12
servo_shaft_cover

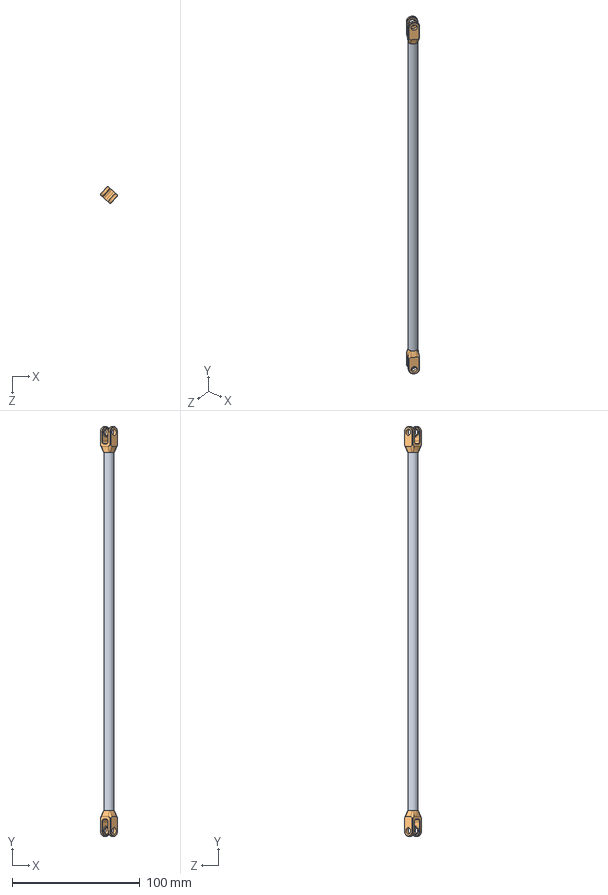
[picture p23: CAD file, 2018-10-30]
mechanical/design/linkage_uni_bearing/arm_clevis_assembly.SLDASM
13.5 x 321.0 x 13.4 mm
8x6 Carbon Tube
clevis x 2

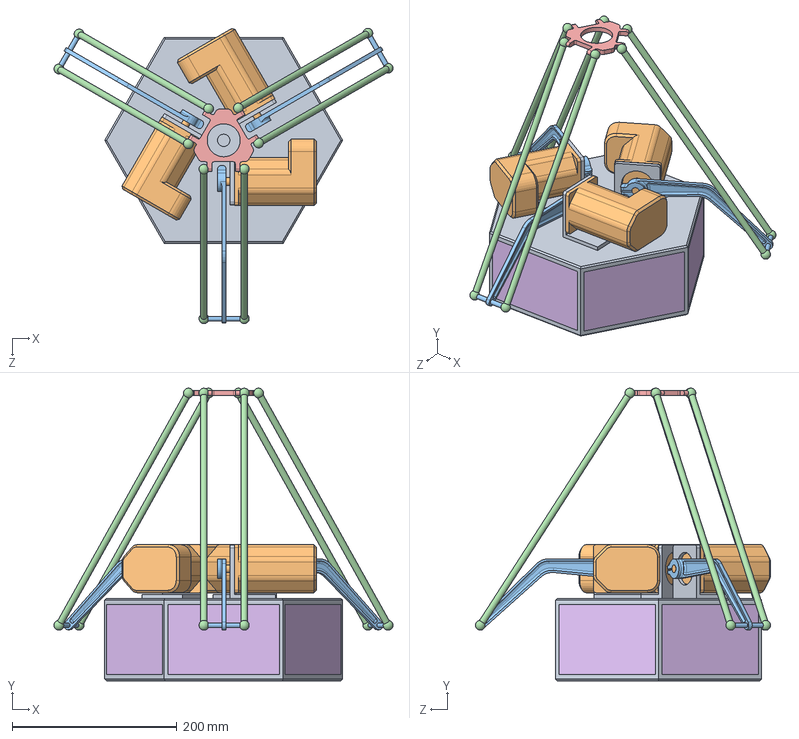
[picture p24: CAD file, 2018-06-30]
mechanical/simplified_geometry/assem_overview_simplified.SLDASM
411.2 x 355.0 x 358.2 mm
base_motors
clearpath_servo x 3
bicep_simplified x 3
forearm_simplified x 6
effector_simplified
simplified_sideplate x 6

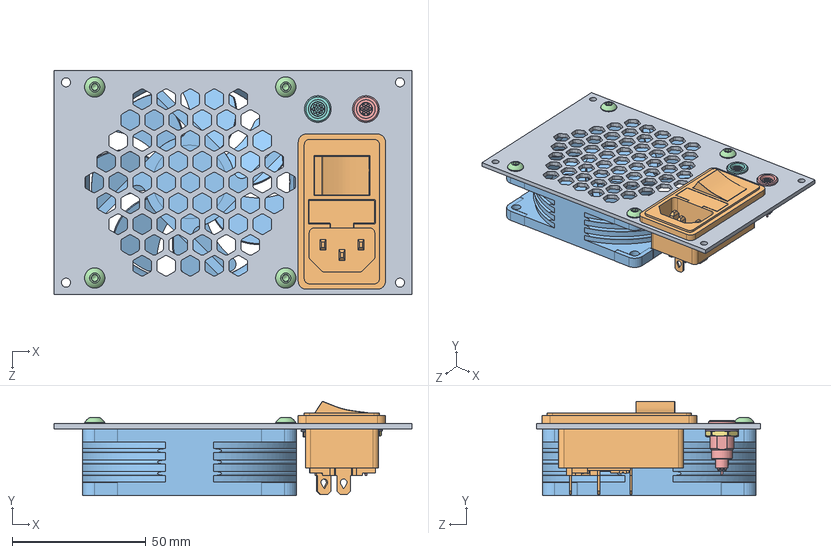
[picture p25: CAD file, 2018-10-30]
mechanical/design/electronics_panel.SLDASM
134.0 x 35.4 x 84.0 mm
side_cover_fan
IEC 320 Switched
Noctua nf-a8-pwm fan 80x80x25
socket button head cap screw_am x 4
egg_0b_307_cll_1
egg_0b_307_cll_2
egg_0b_307_cll_3
egg_0b_309_cll_1
egg_0b_309_cll_2
egg_0b_309_cll_3

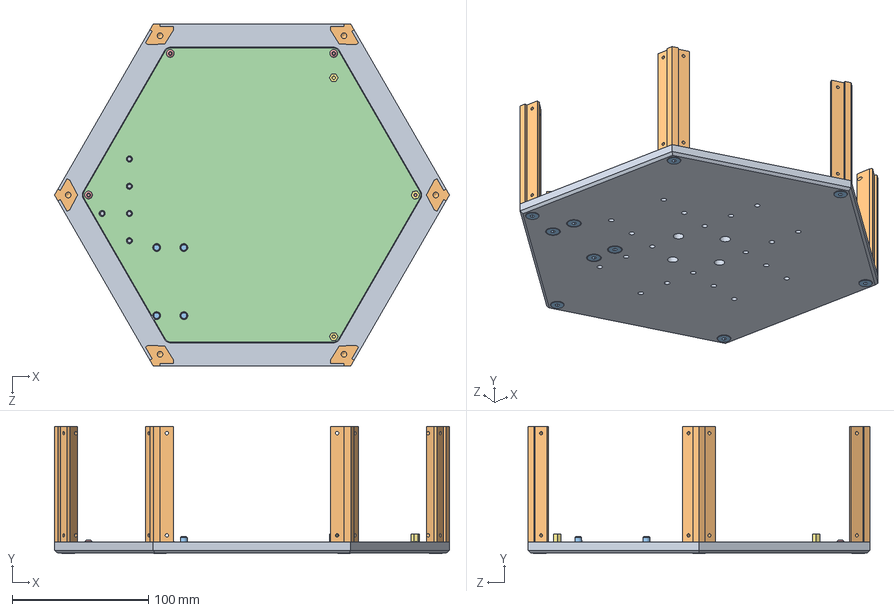
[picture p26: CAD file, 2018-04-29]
mechanical/design/frame_bottom_assembly.sldasm
290.0 x 93.4 x 251.1 mm
bottom_plate_detail
frame_pillar x 6
socket countersunk head screw_am x 10
bottom_plate_cover
socket button head cap screw_am x 3
nutsert_M3 x 6
M3_standoff x 3

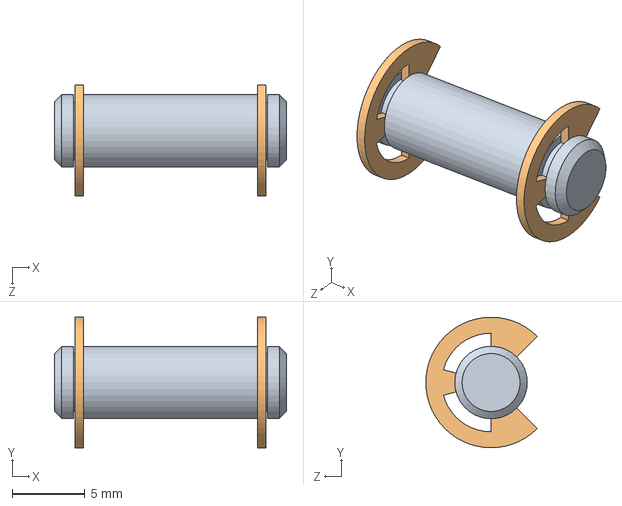
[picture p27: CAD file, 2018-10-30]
mechanical/design/linkage_uni_bearing/CDG5-12.SLDASM
16.0 x 9.00 x 7.68 mm
_CDG5-12D
_No.4_1 x 2

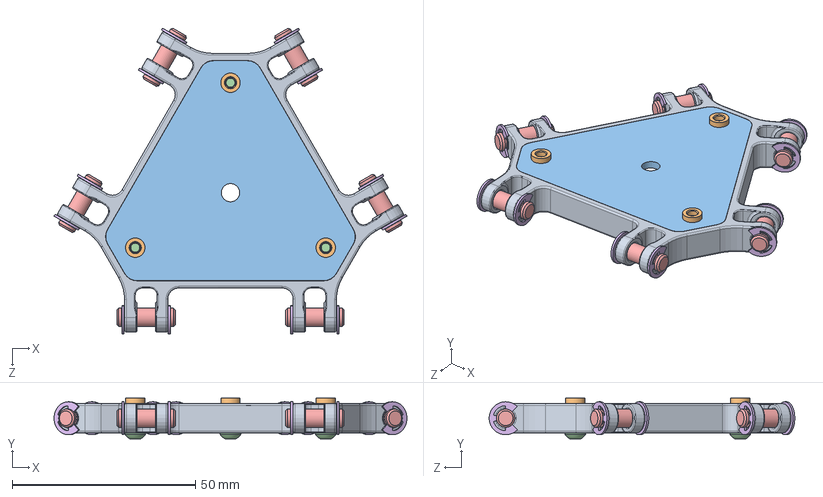
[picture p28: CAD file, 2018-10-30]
mechanical/design/linkage_uni_bearing/effector_assembly.SLDASM
96.3 x 11.1 x 83.4 mm
effector_planar
nutsert_M3 x 3
effector_plate
socket button head cap screw_am x 3
_CDG5-12D x 6
_No.4_1 x 12

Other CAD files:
mechanical/design/cots-modified/pcb/SOIC127P1032X265-16L87.sldasm
mechanical/design/cots-modified/pcb/MOLEX_SABRE_431600102.sldasm
mechanical/design/cots-modified/pcb/MOLEX_MICROFITJR_039281043.sldasm
mechanical/design/cots-modified/pcb/PKMCS0909E4000.sldasm
mechanical/design/base_assembly.SLDASM
mechanical/design/base_plate.SLDPRT
mechanical/design/bicep.SLDPRT
mechanical/design/bicep2.SLDPRT
mechanical/design/bicep_elbow.SLDPRT
mechanical/design/bottom_plate_cover.SLDPRT
mechanical/design/bottom_plate_detail.SLDPRT
mechanical/design/cots-modified/4_pin_motor_loom/39-01-3045.SLDPRT
mechanical/design/cots-modified/4_pin_motor_loom/microfit_2x2_loom.SLDPRT
mechanical/design/cots-modified/8_pin_motor_loom/39-01-3085.SLDPRT
mechanical/design/cots-modified/8_pin_motor_loom/microfit_4x2_loom.SLDPRT
mechanical/design/cots-modified/8x6 Carbon Tube.SLDPRT
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

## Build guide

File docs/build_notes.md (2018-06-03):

# General Build Notes

Steps taken during build, issues and musings for potential future versions.

## Wiring
 
ModDIY Mini-Fit JR wires are probably 100mm too long for optimium wiring inside the enclosure.
The wires also needed to have the heatshrink 'thinned' around the connector where they enter the plug, due to heatshrink stopping full insertion of the pin.

Mains wiring could have been sleeved. Probably could have made it slightly shorter, and used more flexible wiring.

LEMO connectors were a pain to wire by hand. Spend little bit more to get the pre-loomed versions.

## Mechanics
 
Thicker carbon side plates might be a good upgrade to reduce flex in the PSU connector, and improve the weight of the lower section.

Tolerances can be tightened on the carbon plates against the main frame.

The CNC house should have blasted or finished the CNC aluminium before anodizing, the natural grain shows through too much.

The Bicep-Motor shaft connection needs tighter tolerances, the slip on the shaft requires very forceful tightening.

Wiring to the motors could have been improved if the holes were large enough to accept the Mini-fit connector. Alternatively, put a panel mount connector on the top plate, and use a 'external loom' and 'internal loom'.

I probably could have packaged the stack differently, going for a tall shape with 90deg gearboxes on the motors, which would thin out the stack, add some height (and possibly make the PCB a more sane geometry), and allow for longer biceps in the same bench-space. While the gearboxes cost more, that could be offset with smaller clearpath servos for lower power, and would result in higher precision.

## PCB

The PCB power connector and motor connectors should be spaced out slightly more, as the Sabre connectors from the IPC-5 PSU conflict with the motor looms, and the outermost PSU connector actually fouls with the PCB input connector if the locking tabs are installed on both connectors.

For this version, I'm abusing the mating friction/force for the actual spades, and have removed the locking tabs on the Sabre to make things fit.

More mounting holes for better rigidity would have been great, but would be difficult to fit with current layout. Thicker PCB would also help flex.

## Other Thoughts

Fan is quite quiet and could possibly be upgraded to something with a higher flow rate. Positioning could improve to reduce wiring loom clutter internally.

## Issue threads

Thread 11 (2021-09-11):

Libraries Not Found!

WoulaMaker, 2021-09-11:
Hi,

I am trying to open the schematic from Kicad but all components are unvisible (means replaced by a question mark). I think library used in the project is not availabe. Please could you tell me how to fix it or where i could find the library.

Thanks !

Further note : I am using Kicad 5.1.5

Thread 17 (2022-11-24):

Joint consideration

tapir, 2022-11-24:
Super cool robot! I was wondering since the axis of your universal joints are actually offset, do you need to take that into account in your kinematics calculations?

I'm asking because I think this kind of universal joint is the best for a "printed" solution in terms of play (especially with an H7 pin) and life expectancy compared to ball-socket, magnet and traditional universal joints but I'm not sure I have the knowledge to modify my firmware (Klipper) to accoutn for the offset if it makes a difference in kinematics.

Scottapotamas, 2022-11-24:
Just to clarify, are you referring the to 'v1' joint design pictured in the slightly outdated readme image, or the 'v1.1' [that since replaced it](https://electricui.com/blog/delta-bot#whats-next)?

I don't take it into account with the solver in this project, but I did check the the mechanical setup used in this project matched the theoretical solve (Solidworks motion simulation used to compare motor angles against effector positions, compared to IK solves).

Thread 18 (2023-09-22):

Misumi part numbers for the bearing links

RedAnon, 2023-09-22:
Hi,
do you have the part numbers for the Misumi roller follower pins and the retaining rings to match the bearings? It's missing from the documentation.

Thanks

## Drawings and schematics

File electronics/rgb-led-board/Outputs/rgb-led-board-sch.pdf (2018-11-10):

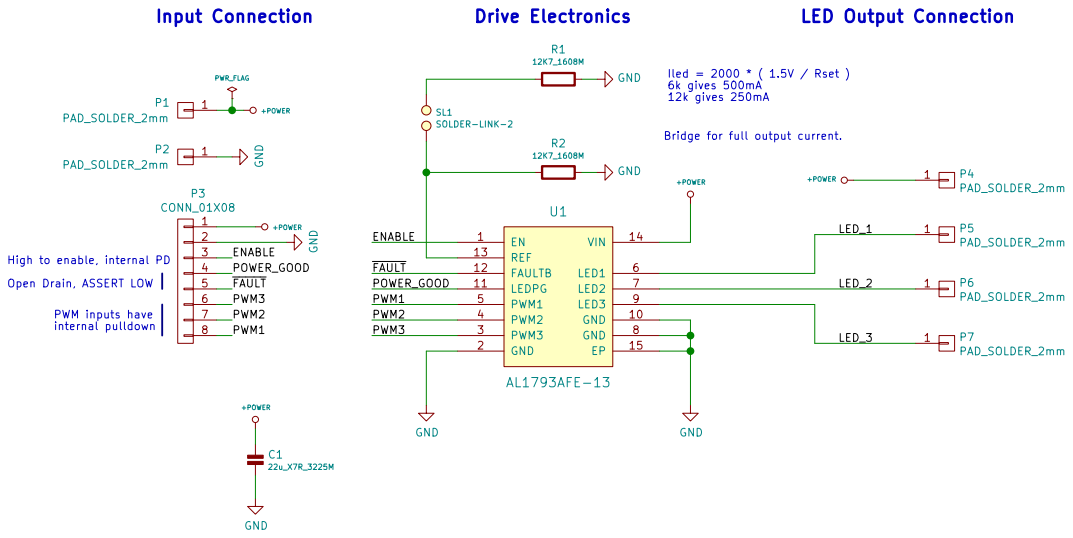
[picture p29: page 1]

12K7_1608M High to enable, internal PD

+POWER
Bridge for full output current. +POWERC1

Open Drain, ASSERT LOW

File: rgb-led-board.sch Sheet: / Electric UI Scott Rapson GND

Id: 1/1 Title: 3-Channel LED driver

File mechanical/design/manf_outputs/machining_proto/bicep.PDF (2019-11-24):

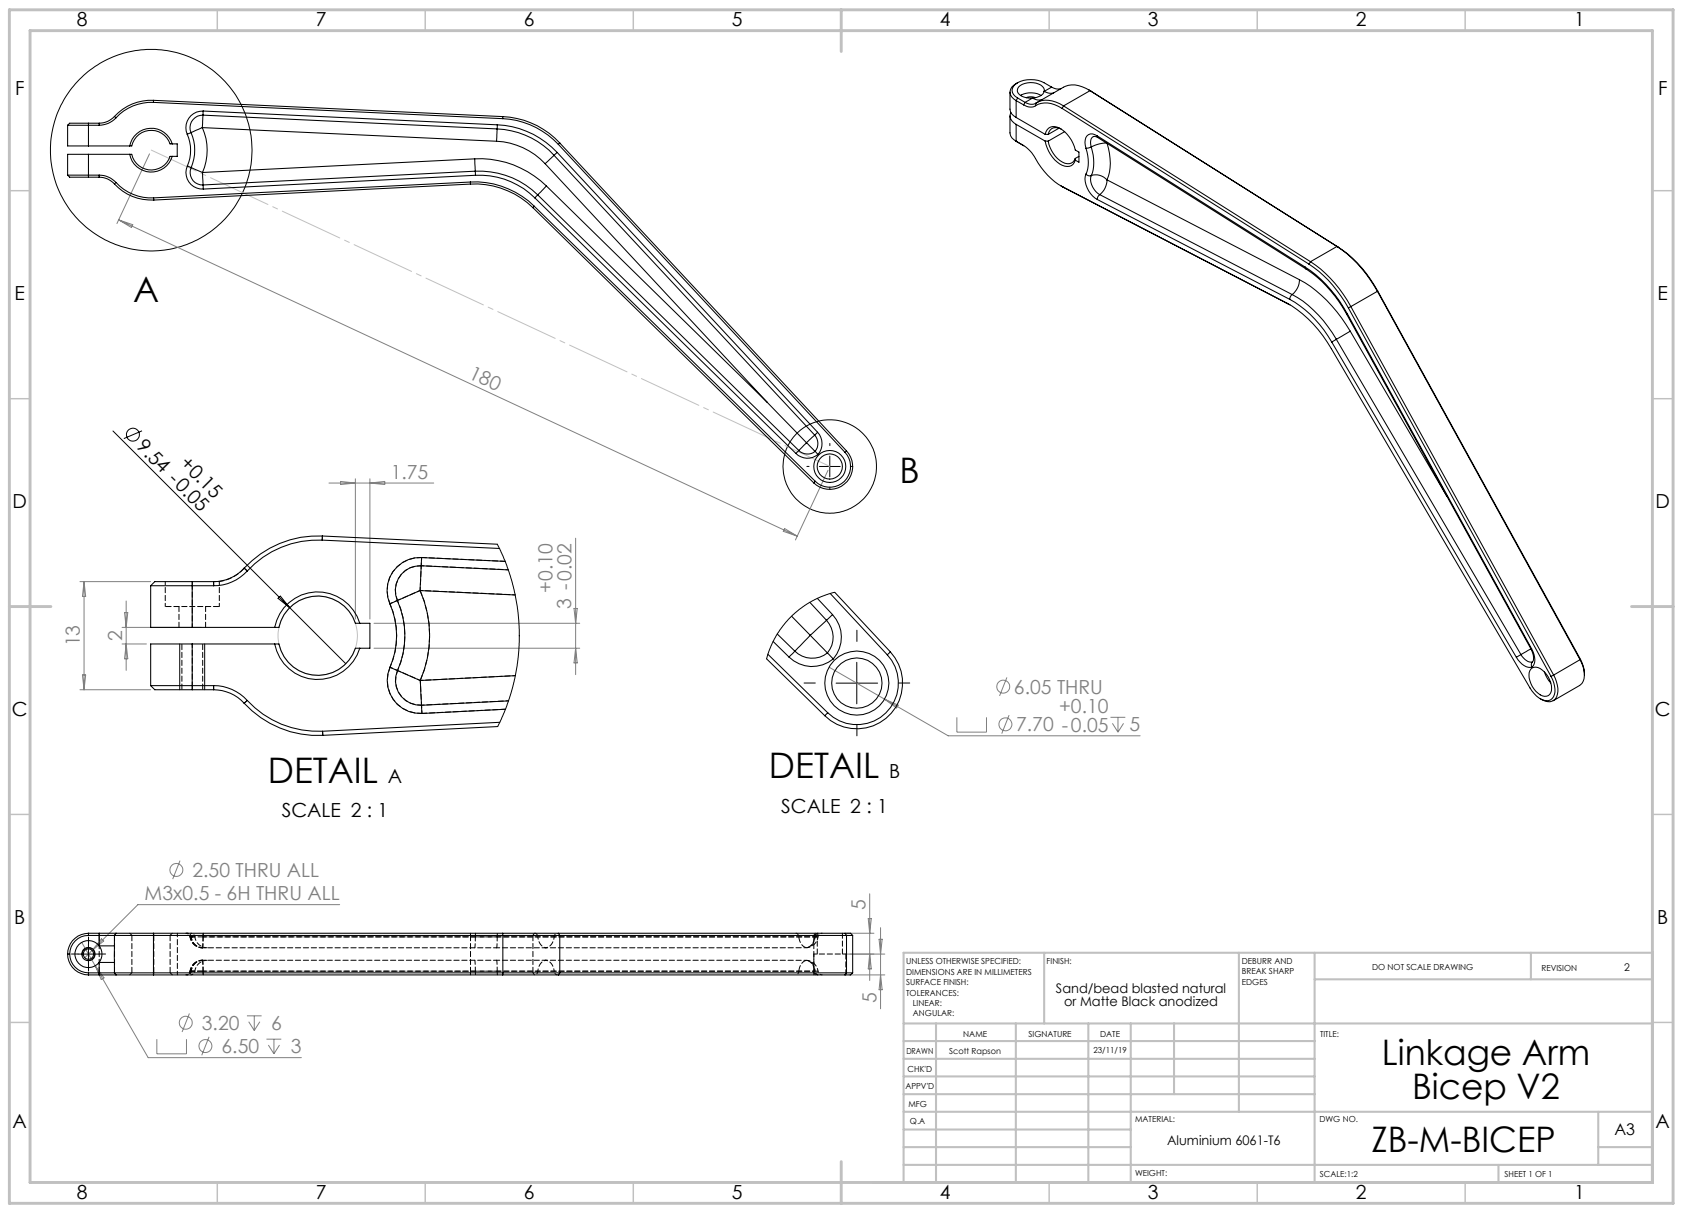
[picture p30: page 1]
DETAIL A; SCALE 2 : 1; 6.05 THRU 0.05 5; DETAIL B; 2.50 THRU ALL M3x0.5 - 6H THRU ALL; FINISH:; DEBURR AND; BREAK SHARP; DO NOT SCALE DRAWING; REVISION; SCALE:1:2; SHEET 1 OF 1

UNLESS OTHERWISE SPECIFIED:
DIMENSIONS ARE IN MILLIMETERS
SURFACE FINISH:
TOLERANCES:
LINEAR:
ANGULAR:

Sand/bead blasted natural
or Matte Black anodized

NAME | SIGNATURE | DATE | | | | TITLE: Linkage Arm Bicep V2

DRAWN | Scott Rapson | | 23/11/19
CHK'D
APPV'D
MFG
Q.A | | | | MATERIAL: | DWG NO. ZB-M-BICEP | A3 Aluminium 6061-T6

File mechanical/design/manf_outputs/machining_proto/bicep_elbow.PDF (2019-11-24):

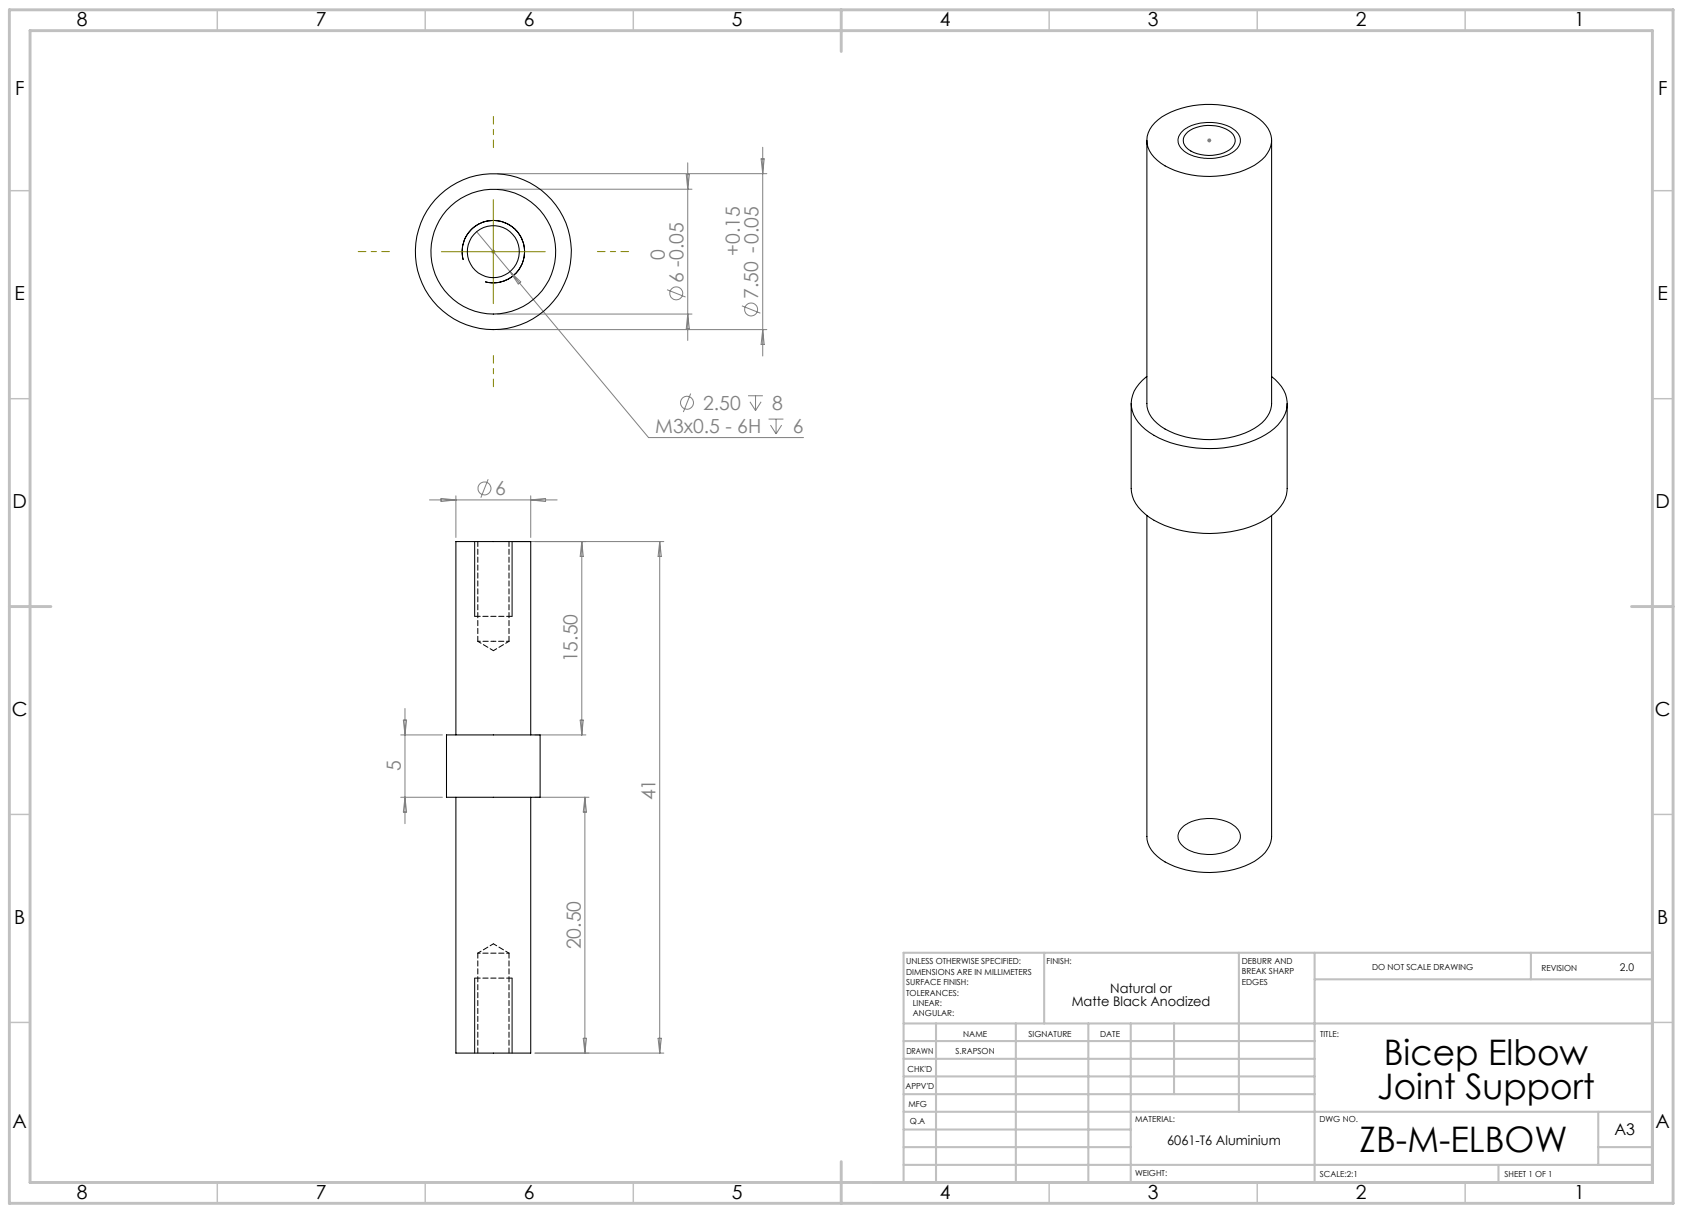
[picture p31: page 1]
FINISH:; DEBURR AND; BREAK SHARP; DO NOT SCALE DRAWING; REVISION; SCALE:2:1; SHEET 1 OF 1

UNLESS OTHERWISE SPECIFIED:
DIMENSIONS ARE IN MILLIMETERS
SURFACE FINISH:
TOLERANCES:
LINEAR:
ANGULAR:

Natural or
Matte Black Anodized

NAME | SIGNATURE | DATE | | | | TITLE: Bicep Elbow Joint Support

DRAWN | S.RAPSON
CHK'D
APPV'D
MFG
Q.A | | | | MATERIAL: | DWG NO. ZB-M-ELBOW | A3 6061-T6 Aluminium

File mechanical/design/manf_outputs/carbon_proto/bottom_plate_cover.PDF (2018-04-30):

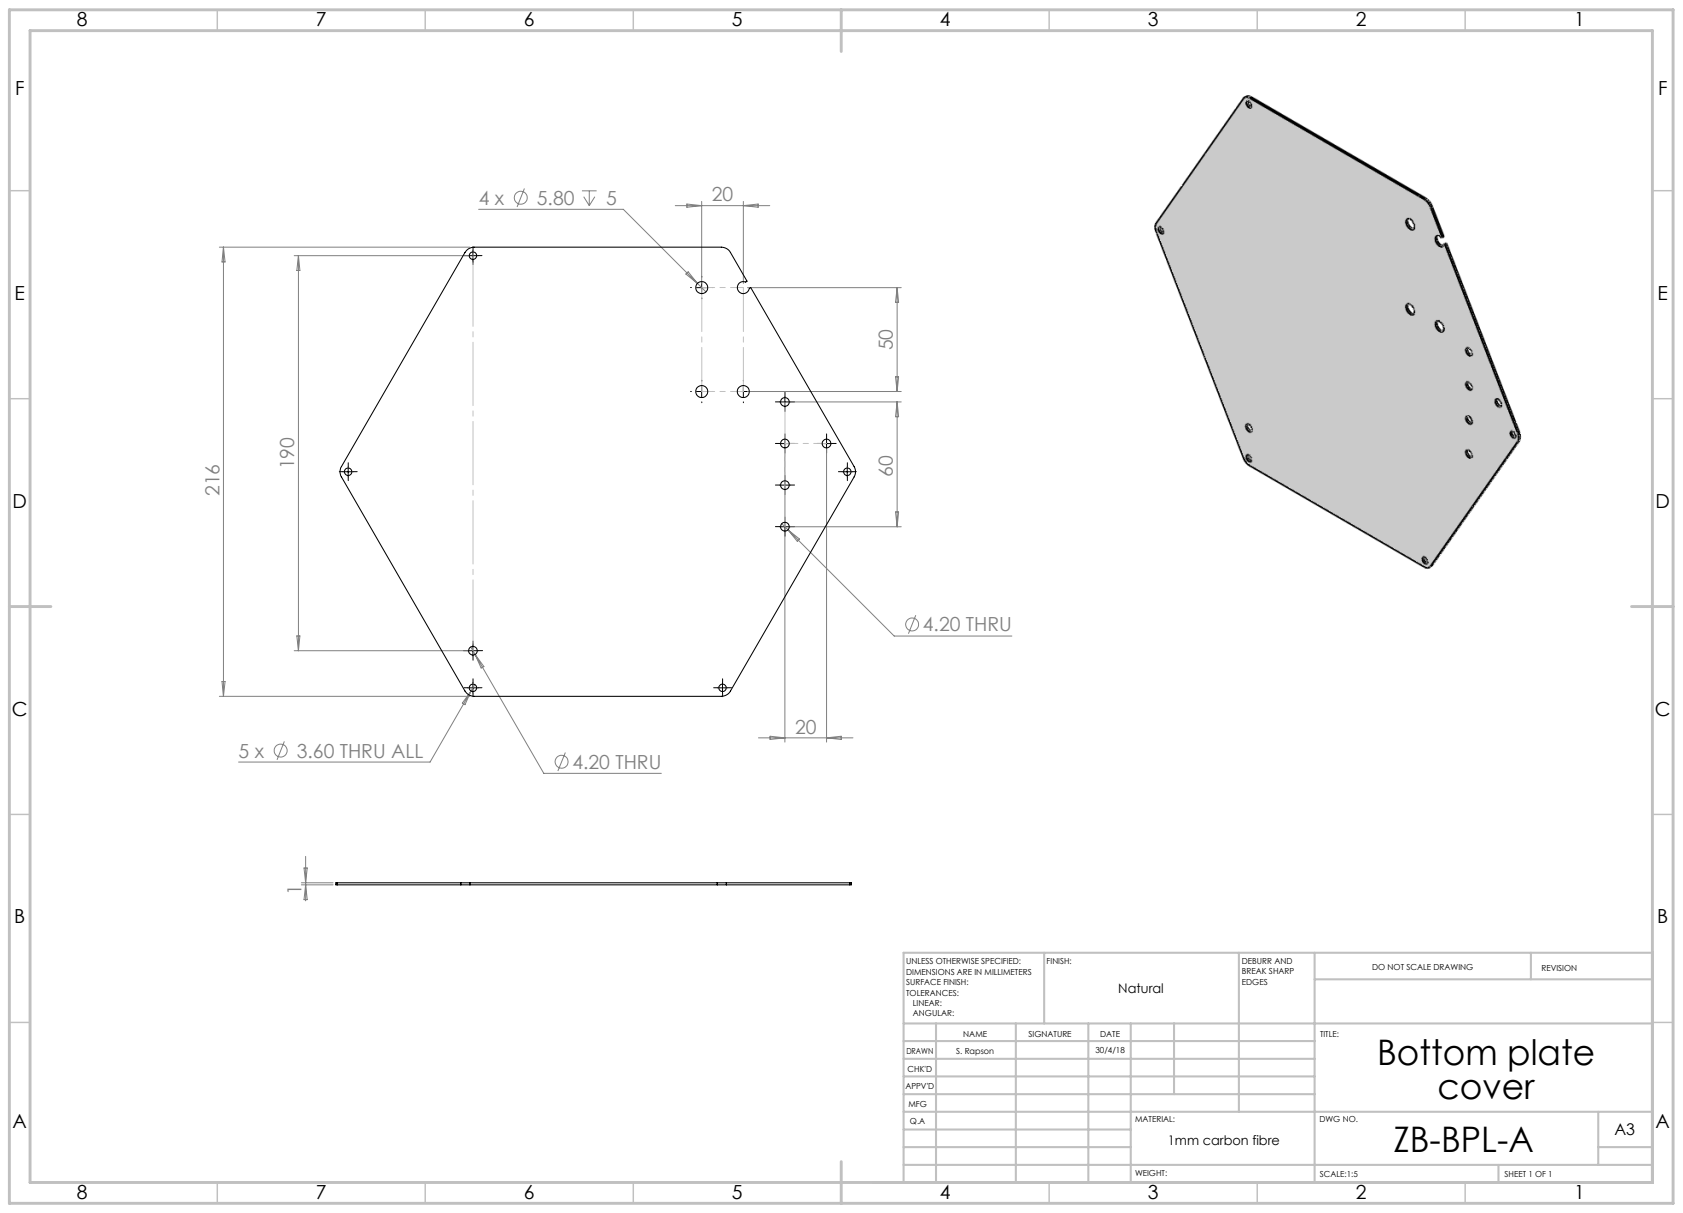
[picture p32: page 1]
3.60 THRU ALL; 4.20 THRU; FINISH:; DEBURR AND; BREAK SHARP; DO NOT SCALE DRAWING; REVISION; SCALE:1:5; SHEET 1 OF 1

UNLESS OTHERWISE SPECIFIED:
DIMENSIONS ARE IN MILLIMETERS
SURFACE FINISH:
TOLERANCES:
LINEAR:
ANGULAR:

NAME | SIGNATURE | DATE | | | | TITLE: Bottom plate cover

DRAWN | S. Rapson | | 30/4/18
CHK'D
APPV'D
MFG
Q.A | | | | MATERIAL: | DWG NO. ZB-BPL-A | A3 1mm carbon fibre

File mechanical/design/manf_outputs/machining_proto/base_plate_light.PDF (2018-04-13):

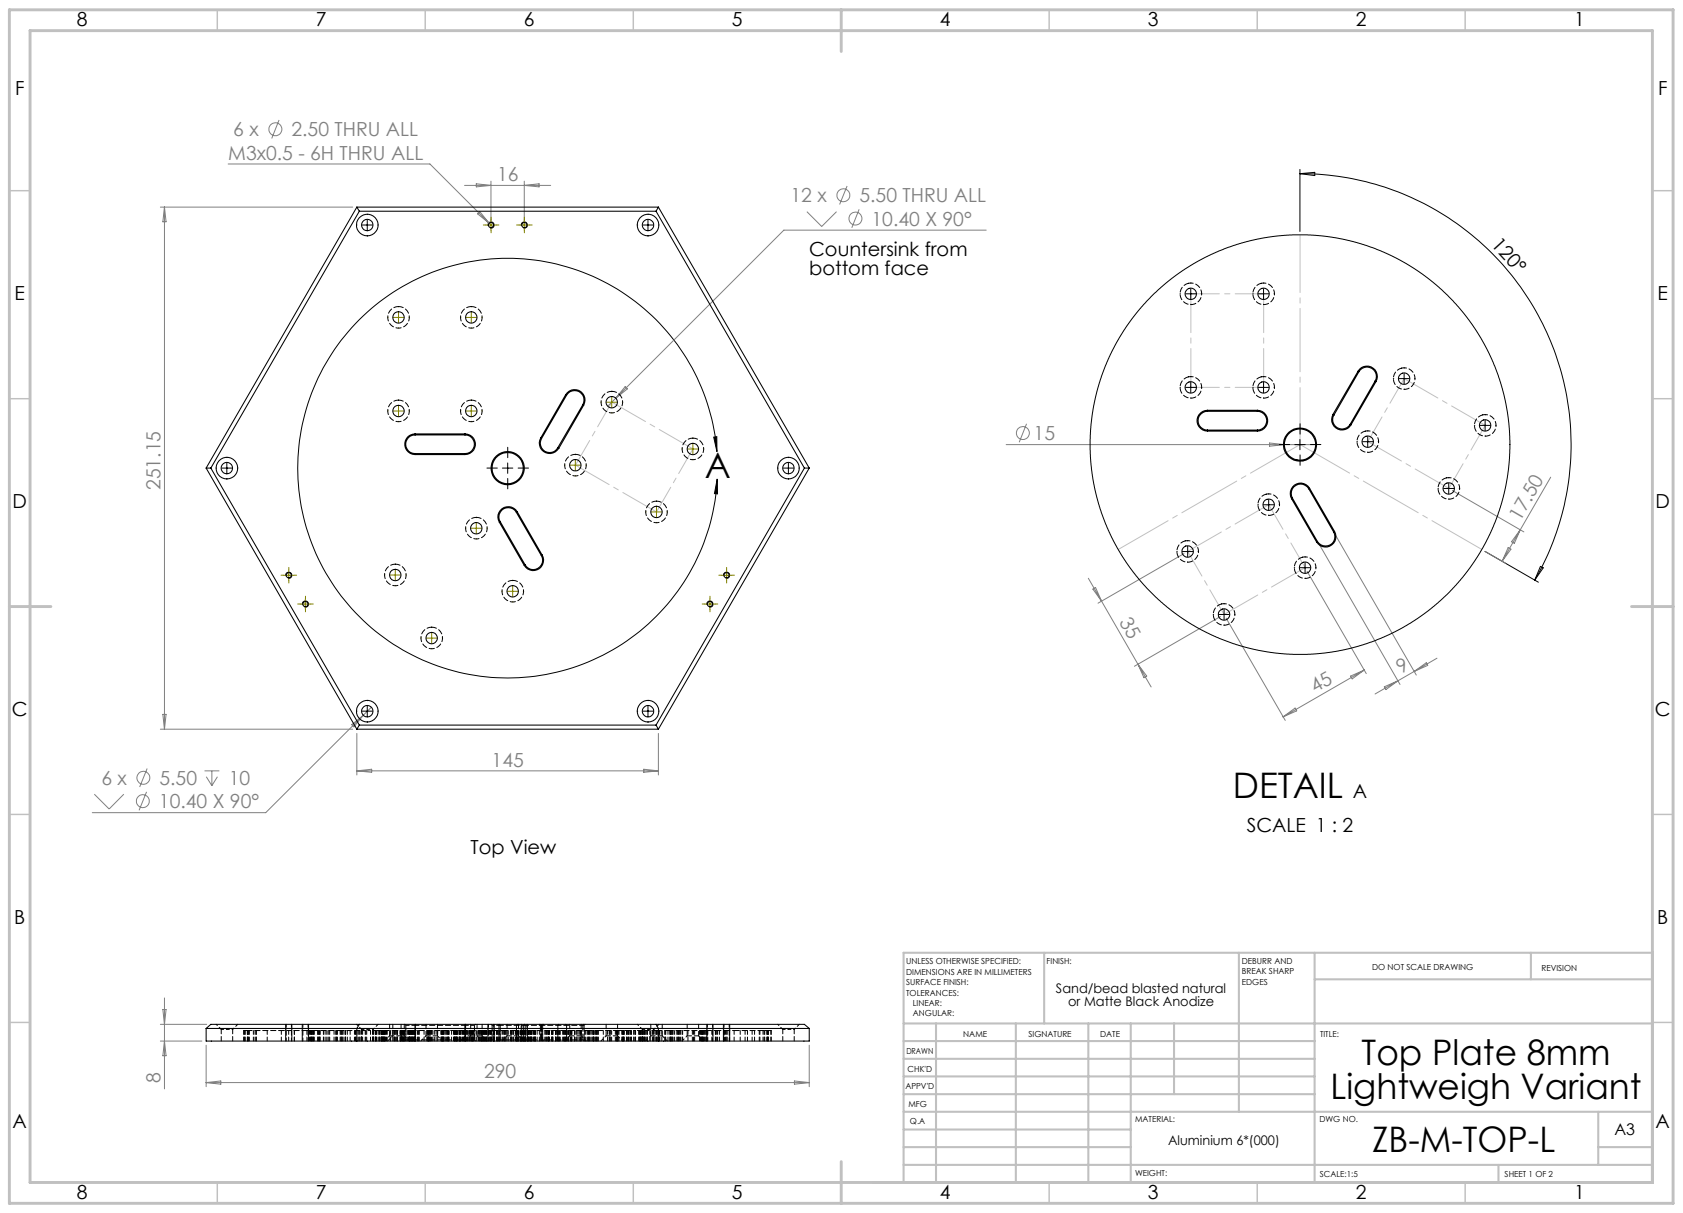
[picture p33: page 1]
2.50 THRU ALL; M3x0.5 - 6H THRU ALL; 5.50 THRU ALL; 10.40 X 90° Countersink from bottom face; Top View; DETAIL A; SCALE 1 : 2; FINISH:; DEBURR AND; BREAK SHARP; DO NOT SCALE DRAWING; REVISION; SCALE:1:5; SHEET 1 OF 2

UNLESS OTHERWISE SPECIFIED:
DIMENSIONS ARE IN MILLIMETERS
SURFACE FINISH:
TOLERANCES:
LINEAR:
ANGULAR:

Sand/bead blasted natural
or Matte Black Anodize

NAME | SIGNATURE | DATE | TITLE: Top Plate 8mm Lightweigh Variant

CHK'D
APPV'D
MFG
Q.A | MATERIAL: | DWG NO. ZB-M-TOP-L | A3 Aluminium 6*(000)

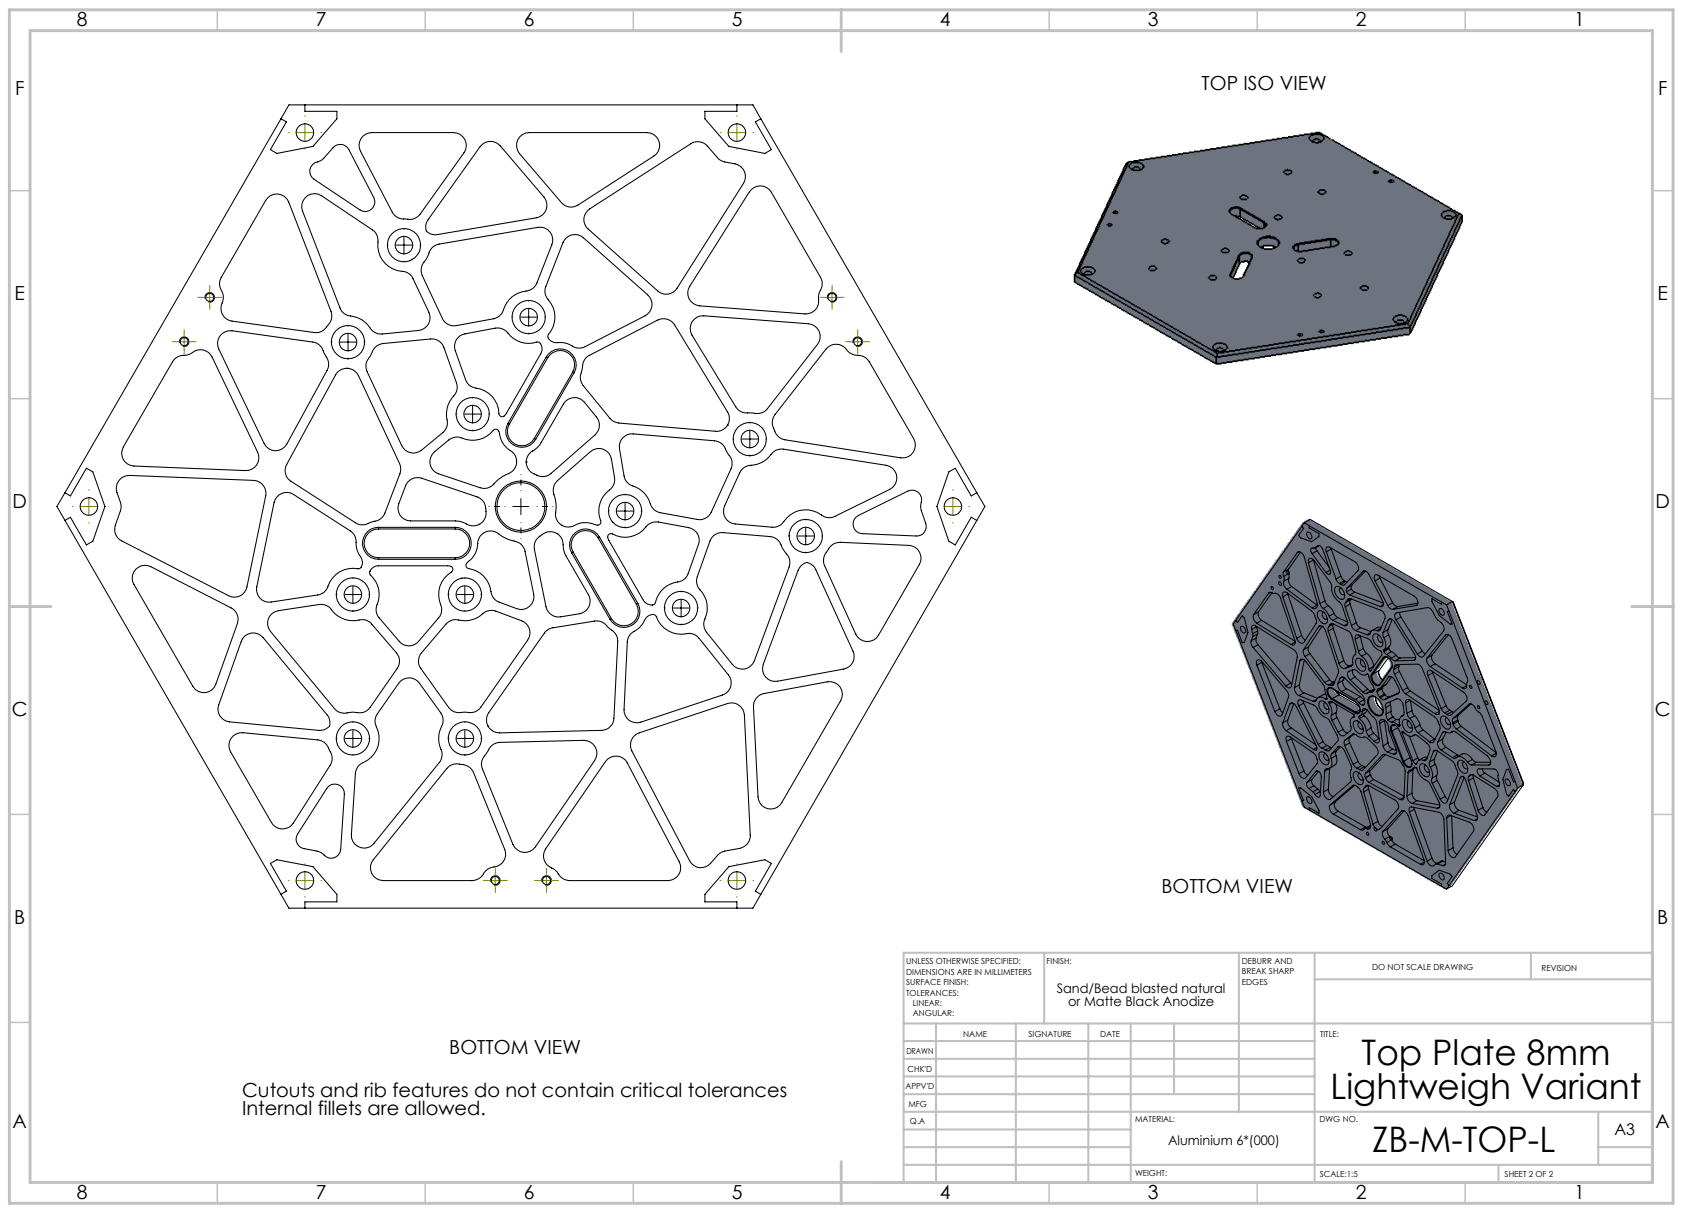
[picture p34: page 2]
BOTTOM VIEW; FINISH:; DEBURR AND; BREAK SHARP; DO NOT SCALE DRAWING; REVISION; SCALE:1:5; SHEET 2 OF 2

TOP ISO VIEW

UNLESS OTHERWISE SPECIFIED:
DIMENSIONS ARE IN MILLIMETERS
SURFACE FINISH:
TOLERANCES:
LINEAR:
ANGULAR:

Sand/Bead blasted natural
or Matte Black Anodize

NAME | SIGNATURE | DATE | | | | TITLE: Top Plate 8mm Lightweigh Variant

DRAWN
CHK'D
APPV'D
MFG
Q.A | | | | MATERIAL: | DWG NO. ZB-M-TOP-L | A3 Aluminium 6*(000)

Cutouts and rib features do not contain critical tolerances
Internal fillets are allowed.

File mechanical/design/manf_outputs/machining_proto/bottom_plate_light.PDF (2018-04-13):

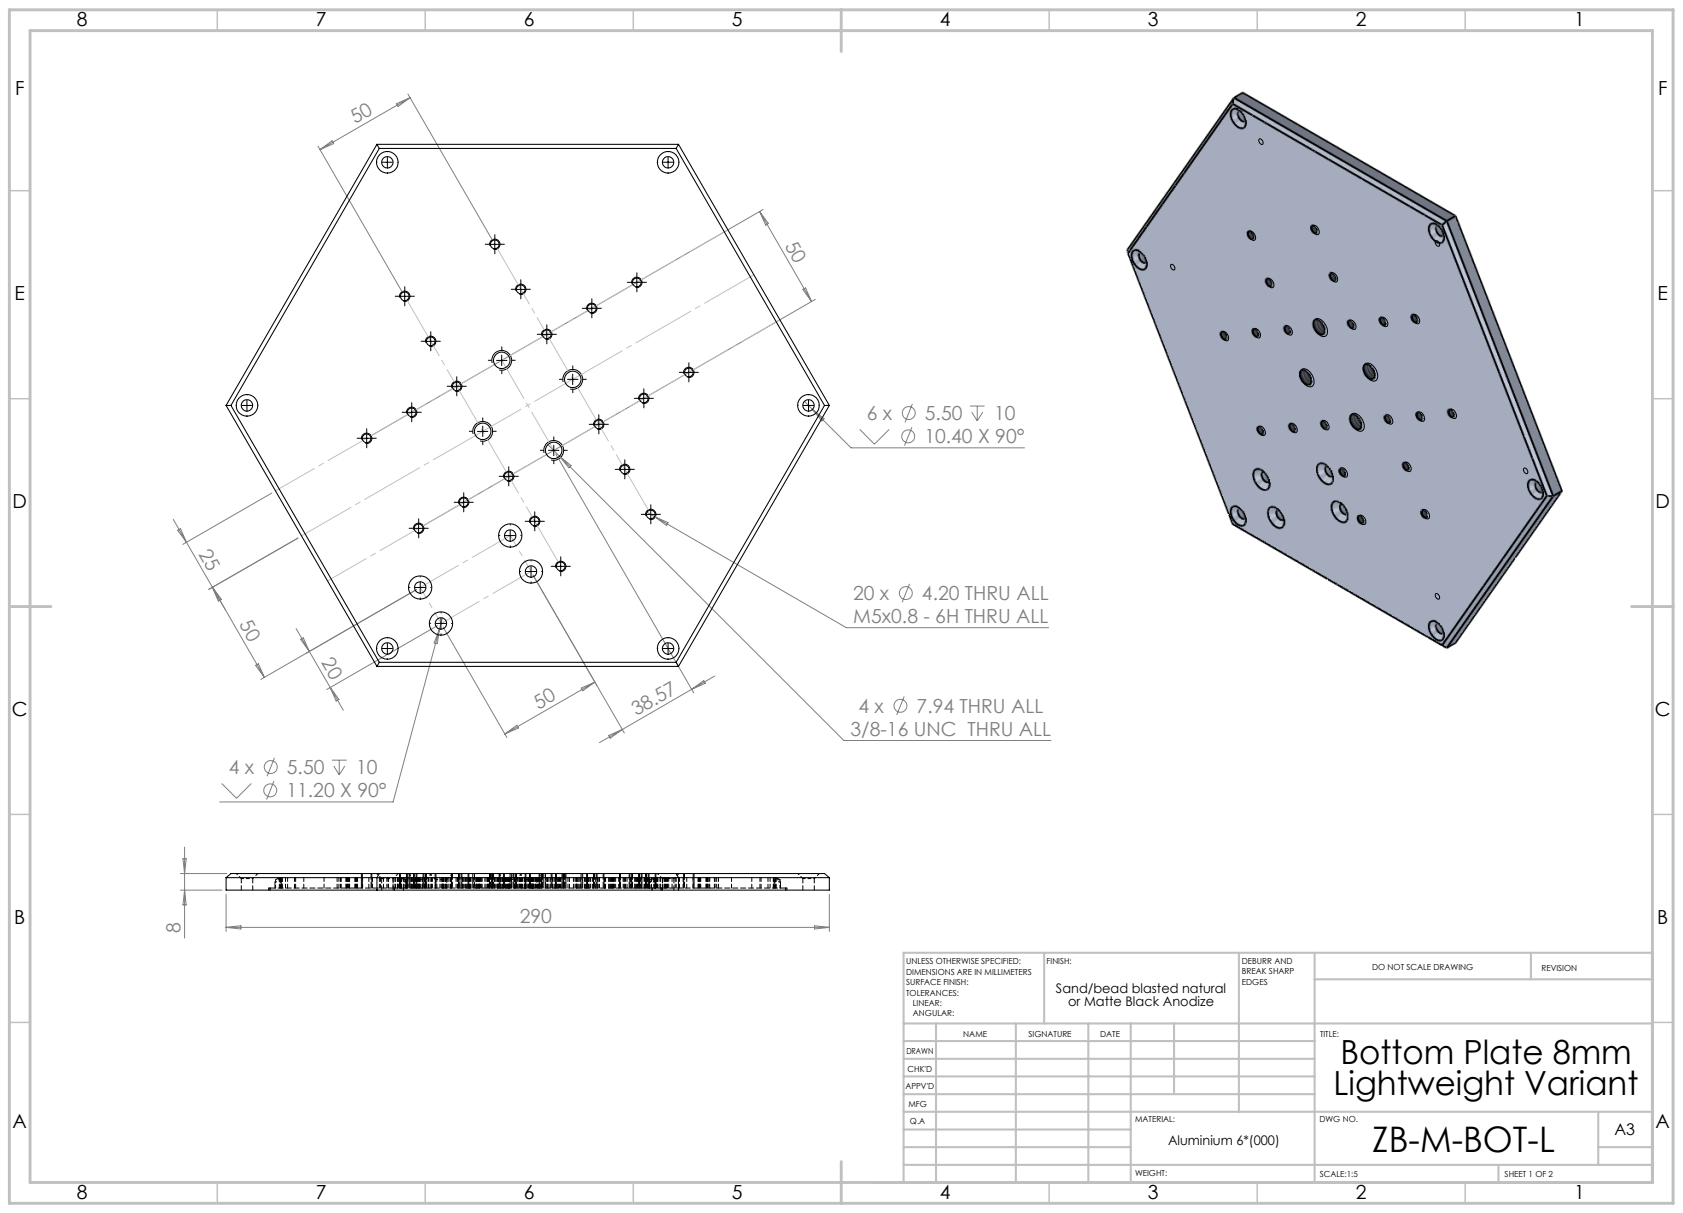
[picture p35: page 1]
4.20 THRU ALL; M5x0.8 - 6H THRU ALL; 7.94 THRU ALL; FINISH:; DEBURR AND; BREAK SHARP; DO NOT SCALE DRAWING; REVISION; SCALE:1:5; SHEET 1 OF 2

3/8-16 UNC THRU ALL

UNLESS OTHERWISE SPECIFIED:
DIMENSIONS ARE IN MILLIMETERS
SURFACE FINISH:
TOLERANCES:
LINEAR:
ANGULAR:

Sand/bead blasted natural
or Matte Black Anodize

NAME | SIGNATURE | DATE | | | | TITLE: Bottom Plate 8mm Lightweight Variant

DRAWN
CHK'D
APPV'D
MFG
Q.A | | | | MATERIAL: | DWG NO. ZB-M-BOT-L | A3 Aluminium 6*(000)

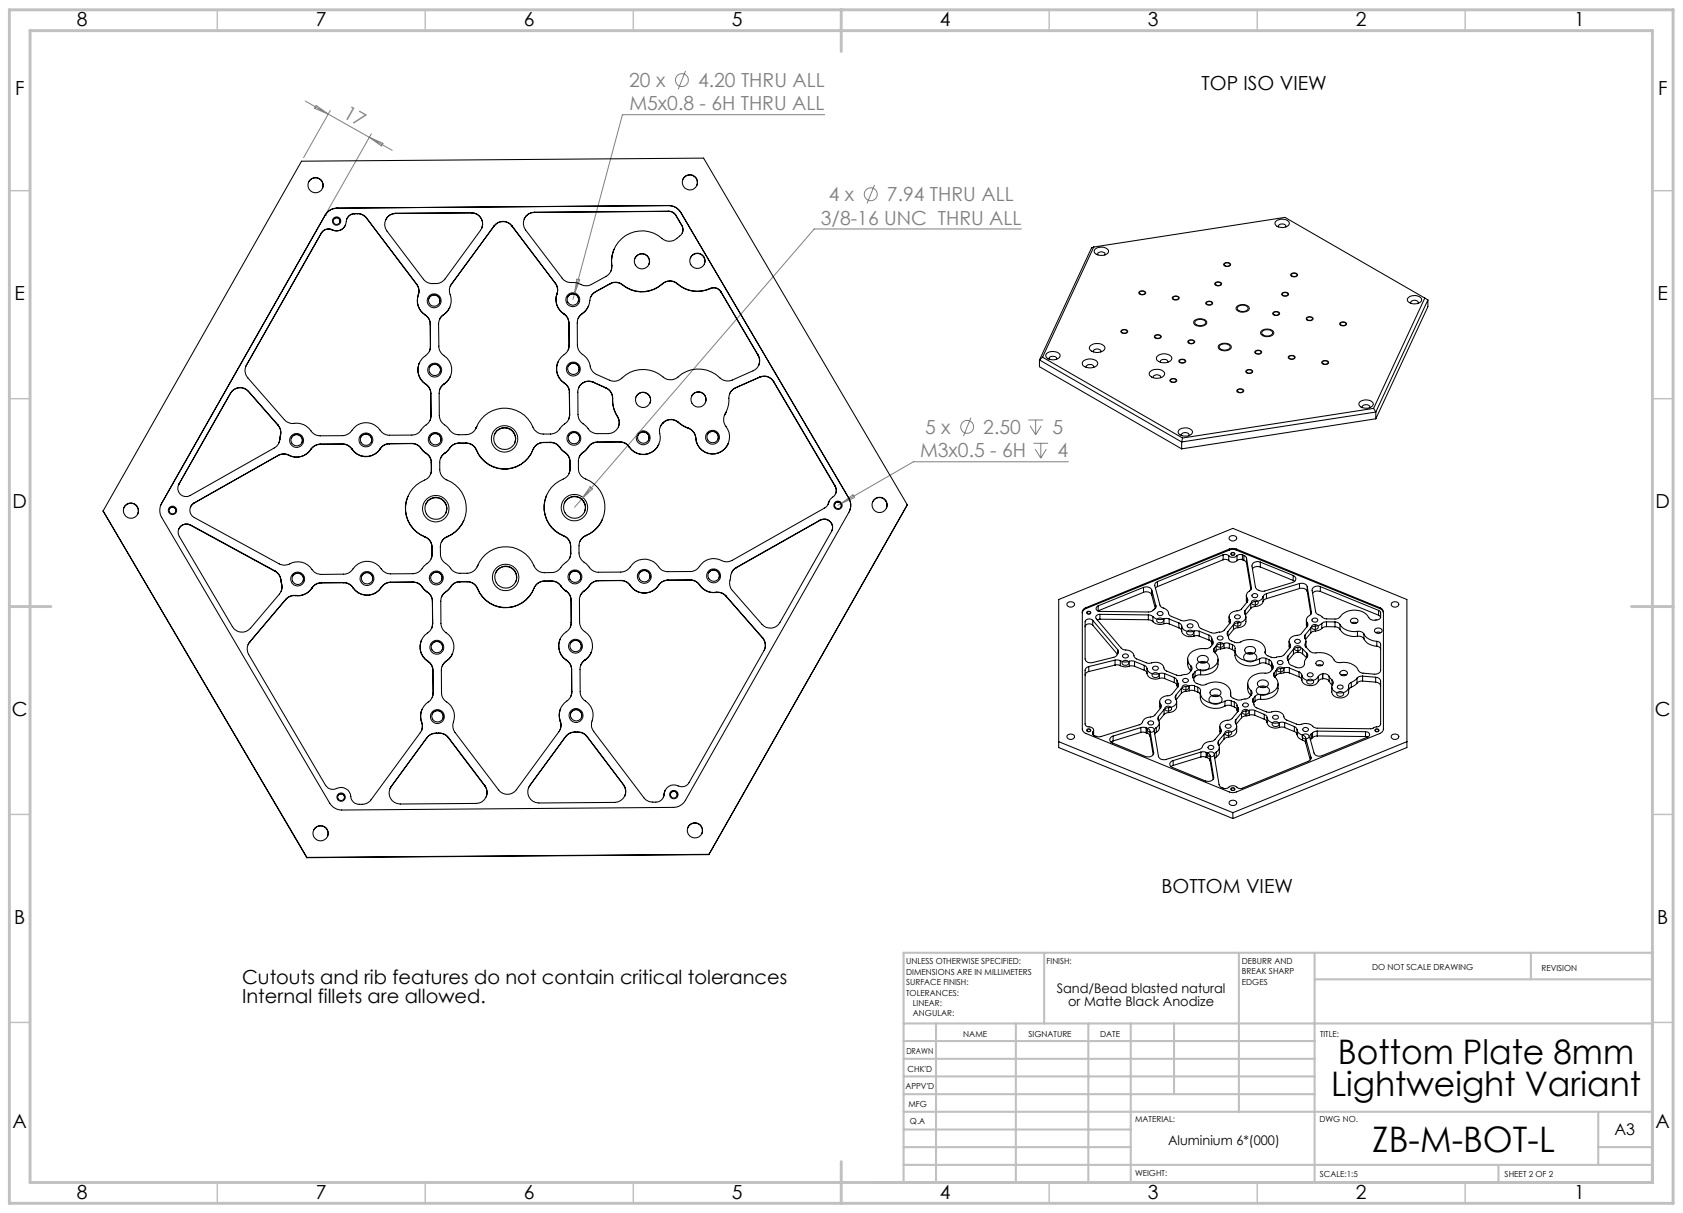
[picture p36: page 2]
4.20 THRU ALL; M5x0.8 - 6H THRU ALL; 7.94 THRU ALL; BOTTOM VIEW; FINISH:; DEBURR AND; BREAK SHARP; DO NOT SCALE DRAWING; REVISION; SCALE:1:5; SHEET 2 OF 2

TOP ISO VIEW

3/8-16 UNC THRU ALL

UNLESS OTHERWISE SPECIFIED:
DIMENSIONS ARE IN MILLIMETERS
SURFACE FINISH:
TOLERANCES:
LINEAR:
ANGULAR:

Sand/Bead blasted natural
or Matte Black Anodize

Cutouts and rib features do not contain critical tolerances
Internal fillets are allowed.

NAME | SIGNATURE | DATE | | | | TITLE: Bottom Plate 8mm Lightweight Variant

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

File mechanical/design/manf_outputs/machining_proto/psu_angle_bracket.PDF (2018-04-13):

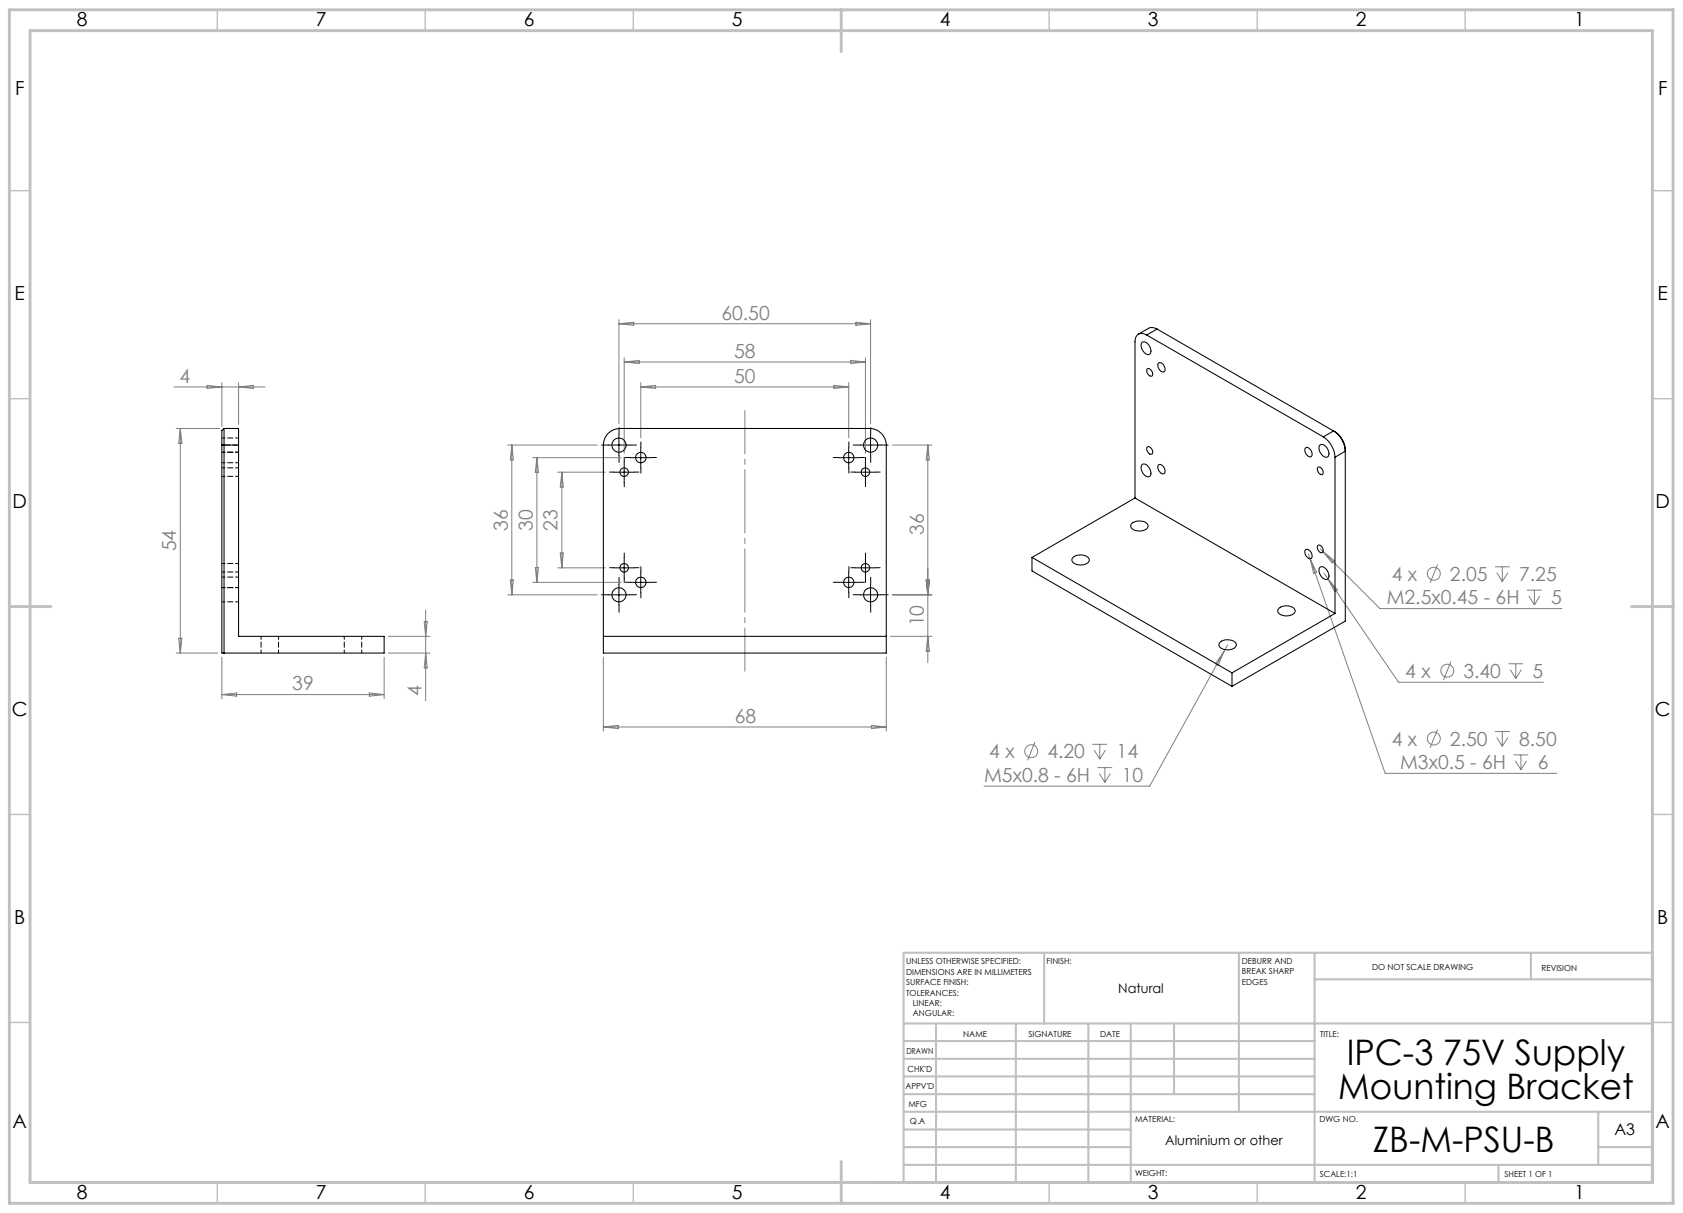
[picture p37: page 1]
FINISH:; DEBURR AND; BREAK SHARP; DO NOT SCALE DRAWING; REVISION; SCALE:1:1; SHEET 1 OF 1

UNLESS OTHERWISE SPECIFIED:
DIMENSIONS ARE IN MILLIMETERS
SURFACE FINISH:
TOLERANCES:
LINEAR:
ANGULAR:

NAME | SIGNATURE | DATE | | | | TITLE: IPC-3 75V Supply Mounting Bracket

DRAWN
CHK'D
APPV'D
MFG
Q.A | | | | MATERIAL: | DWG NO. ZB-M-PSU-B | A3 Aluminium or other

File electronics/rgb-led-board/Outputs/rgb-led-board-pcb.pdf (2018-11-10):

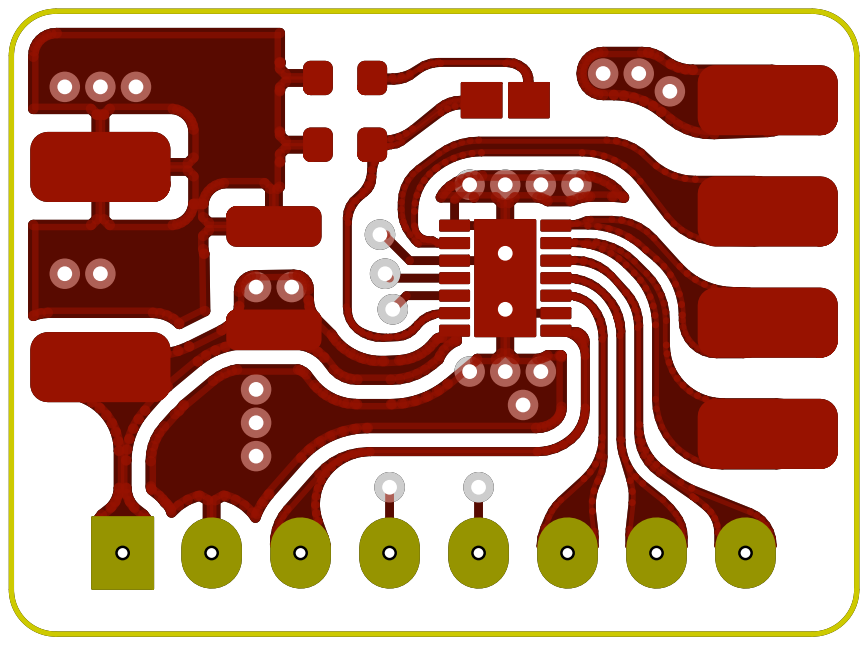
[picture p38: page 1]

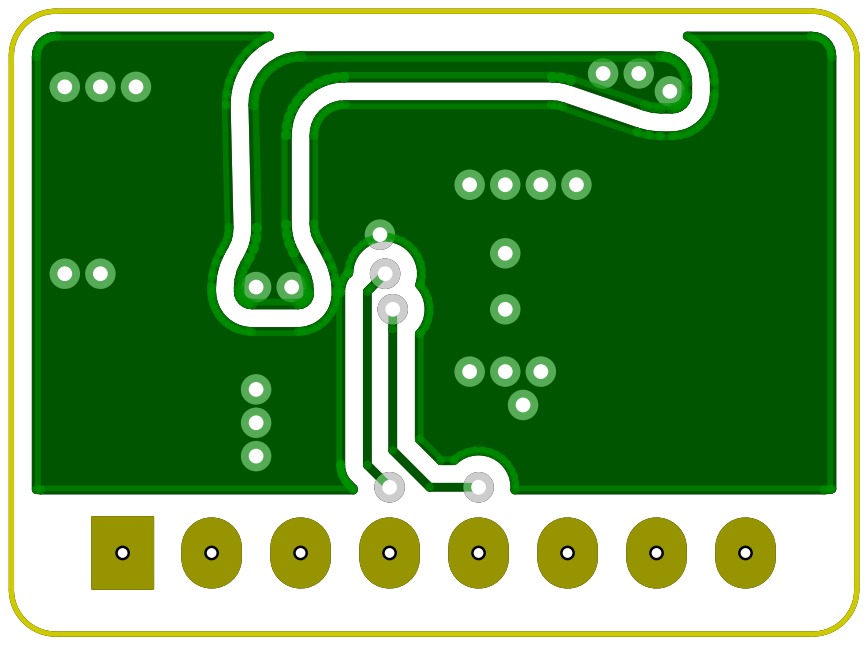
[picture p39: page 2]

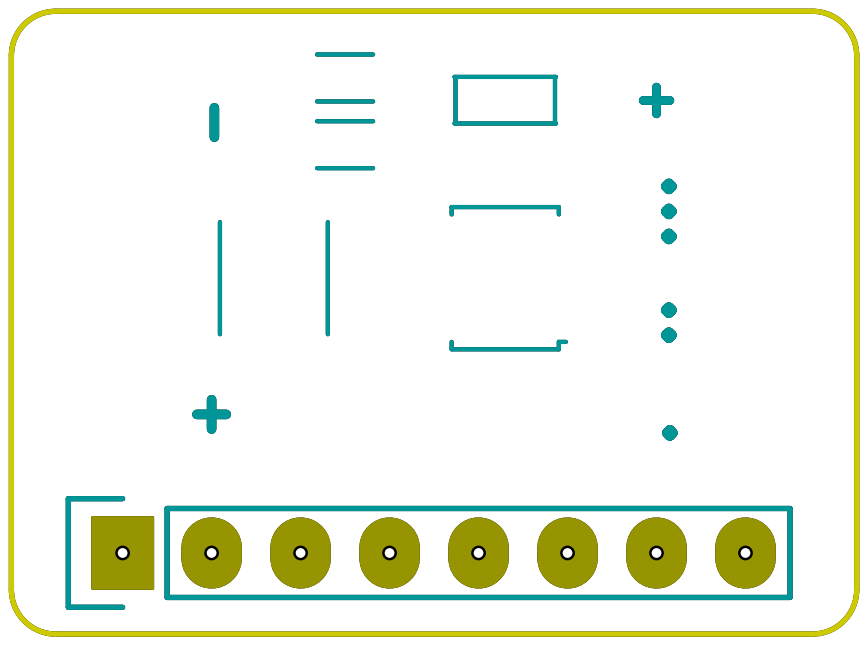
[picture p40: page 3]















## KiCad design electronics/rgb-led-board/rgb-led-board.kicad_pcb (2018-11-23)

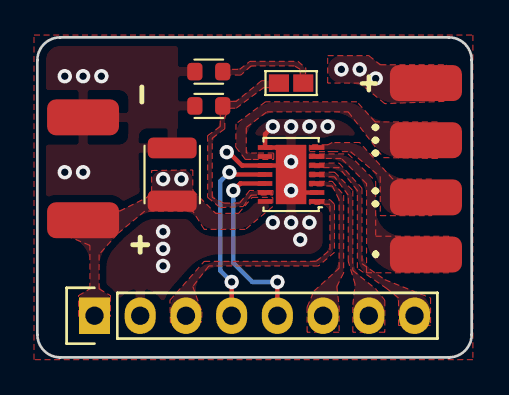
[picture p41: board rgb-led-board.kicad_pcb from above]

Board: 2 copper layers, 24.1 x 17.8 mm, 12 parts (0 on the bottom side), 13 nets.

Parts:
C1: 22u_X7R_3225M; CAPC3225X170N
P1, P2, P4, P5, P6, P7: PAD_SOLDER_2mm
P3: CONN_01X08; 61300811121
R1, R2: 12K7_1608M; RESC1608X50N
SL1: SOLDER-LINK-2; SJ1608-2N
U1: AL1793AFE-13; QFN14P50_400X300X65L40X25N

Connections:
+POWER: C1.1, P1.1, P3.1, P4.1, U1.14
/ENABLE: P3.3, U1.1
/LED_1: P5.1, U1.6
/LED_2: P6.1, U1.7
/LED_3: P7.1, U1.9
/POWER_GOOD: P3.4, U1.11
/PWM1: P3.8, U1.5
/PWM2: P3.7, U1.4
/PWM3: P3.6, U1.3
/~FAULT: P3.5, U1.12
GND: C1.2, P2.1, P3.2, R1.2, R2.2, U1.2, U1.8, U1.10, U1.15
unnamed: R1.1, SL1.1
unnamed: R2.1, SL1.2, U1.13

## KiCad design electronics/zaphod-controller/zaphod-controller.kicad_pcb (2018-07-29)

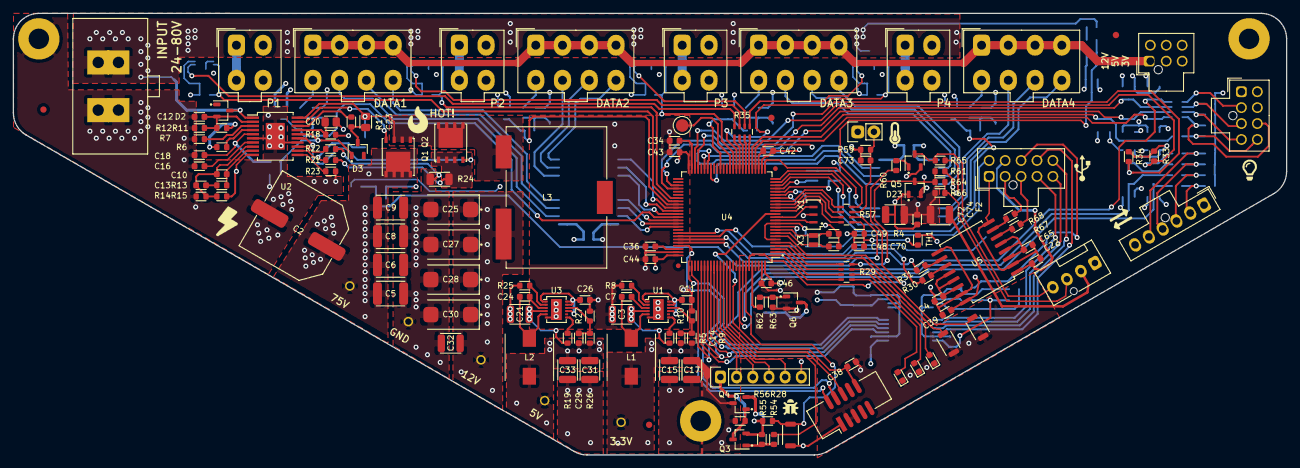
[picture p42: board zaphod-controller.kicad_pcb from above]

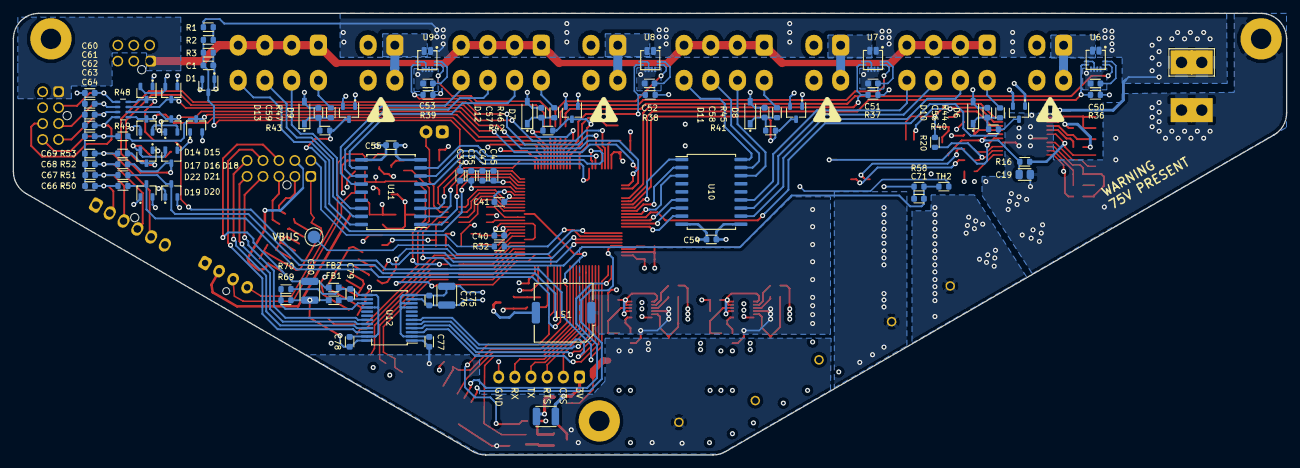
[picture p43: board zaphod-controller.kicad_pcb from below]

Board: 4 copper layers, 199.9 x 69.3 mm, 251 parts (97 on the bottom side), 182 nets.

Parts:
C1, C4, C7, C16, C22, C24, C37, C38, C39, C40, C41, C42, C43, C44, C46, C47, C50, C51, C52, C53, C54, C55, C65, C70, C71, C73, C74, C76, C77, C78, C79: 100n_X7R_1608M; CAPC1608X90N
C2: 47u_ELEC_100V_1350X1350M; CAPAE1350X1350D1490DD450L470N
C3, C21, C75, C80: 10u_X7R_3225M; CAPC3225X170N
C5, C6, C8, C9: 2u2_X7R_4532M; CAPC4532X180N
C10: 15p_X7R_1608M; CAPC1608X90N
C11, C12, C26, C34, C35, C36, C45: 1u_X7R_1608M; CAPC1608X90N
C13: 1n5_X7R_1608M; CAPC1608X90N
C14, C29, C48, C49: 22p_X7R_1608M; CAPC1608X90N
C15, C17, C31, C32, C33, C72: 22u_X7R_3225M; CAPC3225X170N
C18: 330p_X7R_1608M; CAPC1608X90N
C19, C20, C23: 1u_X7R_2012M; CAPC2012X110N
C25, C27, C28, C30: 47u_TANT_7343M; CAPPM7343X310N
C56, C57, C58, C59: 10n_X7R_1608M; CAPC1608X90N
C60, C61, C62, C63, C64, C66, C67, C68, C69: 1n_X7R_1608M; CAPC1608X90N
D1, D6, D7, D8, D9, D14, D15, D16, D17, D18, D19, D20, D21, D22, D23: BAV99; SOT95P240X110-3L16N
D2, D3: 200V_350mW_SOT23; SOT95P240X110-3L16N
D4: LED_YELLOW_1608M; LEDC1608X80L40N
D5: LED_GREEN_1608M; LEDC1608X80L40N
D10, D11, D12, D13: 3V3; SOD3715X145N
D24: LED_RED_1608M; LEDC1608X80L40N
F1, F2: 0.5A_1210L_PTC; FUSC3225X85L50N
FB1, FB2: 1K_1608M; INDC1608X95N
FID1, FID2, FID3, FID4: FIDUCIAL; FID100X200
L1, L2: 22u_MCSDRH73B; INDM7373X355L170X207N
L3: 10u2_PA2050; PULSE_PA2050
LOGO1: LOGO; PANIC_LOGO890X810
LOGO2: LOGO; BUG_LOGO250X250
LOGO3: LOGO; BULB_LOGO230X330
LOGO4: LOGO; THERMO_LOGO_170X350
LOGO5: LOGO; USB_LOGO410X250
LOGO6, LOGO7, LOGO8, LOGO9: LOGO; WARN_TRIANGLE_LOGO440X400
LOGO10: LOGO; WARN_TRIANGLE_LOGO440X400_MASK
LOGO11: LOGO; FIRE_LOGO_320X420
LOGO12: LOGO; BOLT_LOGO_310X490
LOGO13: LOGO; DUPLEX_LOGO330X260
LS1: PKMCS0909E4000-R1; MURATA_PKMCS0909E4000
MNT1, MNT2, MNT3: MNT_M3_PLATED; MTGP650H330
P1: MOLEX_43160-0102; Molex_Sabre_43160-0102_VERT
P2, P3, P4, P5: MOLEX_MINIFIT_JR_2x2_WAY; Molex_Mini-Fit_Jr_5566-04A_2x02_P4.20mm_Vertical
P11, P12, P13, P14: MOLEX_MINIFIT_JR_2x4_WAY; Molex_Mini-Fit_Jr_5566-08A_2x04_P4.20mm_Vertical
P15: MOLEX_NANOFIT_2x4_WAY; Molex_Nano-Fit_105310-xx08_2x04_VERT
P16: MOLEX_NANOFIT_1x6_WAY; Molex_Nano-Fit_105309-xx06_1x06_VERT
P17: MOLEX_NANOFIT_2x3_WAY; Molex_Nano-Fit_105310-xx06_2x03_VERT
P18: CONN_01X02; 61300211121
P19: MOLEX_KK2.54_1x4_WAY_FAN; MOLEX_47053-1000
P20: CONN_01X06; 61300611121
P21: MOLEX_NANOFIT_2x5_WAY; Molex_Nano-Fit_105310-xx10_2x05_VERT
Q1, Q2: Si7852DP; SON127P490X575X90-9T313X381N
Q3, Q6: 2N7002P; SOT95P240X110-3L16N
Q4: NTR1P02T1G; SOT95P240X110-3L16N
Q5: BC847B; SOT95P240X110-3L16N
R1, R2: 130K_1608M; RESC1608X50N
R3, R23, R36, R37, R38, R39, R55, R56, R61, R63, R70: 10K0_1608M; RESC1608X50N
R4, R58, R59: 2K40_1608M; RESC1608X50N
R5, R8, R9, R19, R25, R28: 100K_1608M; RESC1608X50N
R6: 1M_1608M; RESC1608X50N
R7, R27: 12K7_1608M; RESC1608X50N
R10, R44, R45, R46, R47: 22K_1608M; RESC1608X50N
R11: 102K_1608M; RESC1608X50N
R12: 9K53_1608M; RESC1608X50N
R13: 39K_1608M; RESC1608X50N
R14: 1K2_1608M; RESC1608X50N
R15: 10K7_1608M; RESC1608X50N
R16: 750K_1608M; RESC1608X50N
R17: 2R2_1608M; RESC1608X50N
R18: 1R0_1608M; RESC1608X50N
R20, R21, R22: 0R_1608M; RESC1608X50N
R24: R01_3216M; RESC3216X140N
R26: 91K_1608M; RESC1608X50N
R29, R35, R57: 1K_QUAD_ARRAY_1608M; R_Array_Concave_4x1608M
R30, R31, R67, R68: 22R_1608M; RESC1608X50N
R32, R40, R41, R42, R43, R50, R51: 100R_1608M; RESC1608X50N
R33, R34, R65, R66: 4K7_1608M; RESC1608X50N
R48: 47R_QUAD_ARRAY_1608M; R_Array_Concave_4x1608M
R49, R52, R53, R54, R62: 10R_1608M; RESC1608X50N
R60: 1K00_1608M; RESC1608X50N
R64: 33K2_1608M; RESC1608X50N
R69: 16K9_1608M; RESC1608X50N
SW1, SW2, SW3: B3U-1000P_SPST-NO_SMD; B3U-1000P
TEST1: CLIP_HOOK_BROWN; KEYSTONE_5115
TEST2: CLIP_HOOK_YELLOW; KEYSTONE_5004
TEST3: CLIP_HOOK_RED; KEYSTONE_5000
TEST4: CLIP_HOOK_ORANGE; KEYSTONE_5003
TEST5: CLIP_HOOK_BLACK; KEYSTONE_5001
TEST6, TEST8: PROBE_PAD; TP200
TH1, TH2: NTC_10K_1608M; RESC1608X50N
U1, U3: ISL85410FRZ; QFN50P400X300X100-13T170X330N
U2: LM5116; SOP21P65_720X780X200L75X30N
U4: STM32F429VET6; QFP50P1600X1600X160-100L25N
U5: ADUM3160; SOIC127P1032X265-16L87N
U6, U7, U8, U9: ACS711KEXLT_15AB; ACS-EX-12
U10, U11: ULN2003A; SOIC127P1030X265-18L87N
U12: ADUM5412; SOP65P780X200-24L40N
X1: CSTCE8M00G55Z; OSCSC-CSCTE-CERALOCK
X2: SWD_SMT_SOCKET; CNCTECH_3220-10-0300-00
X3: ABS06-107-32.768KHZ; XTALDFN200X120X60-2N

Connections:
+3.3V: C14.1, C15.1, C17.1, C35.1, C37.1, C39.2, C40.1, C41.1, C42.1, C43.1, C44.1, C45.1, C46.1, C47.1, C50.2, C51.2, C52.2, C53.2, C77.2, D1.2, D6.2, D7.2, D8.2, D9.2, D14.2, D15.2, D16.2, D17.2, D18.2, D19.2, D20.2, D21.2, D22.2, D23.2, L1.1, P15.6, P16.1, P17.3, P18.1, Q4.3, R9.1, R33.2, R34.1, R36.2, R37.2, R38.2, R39.2, R56.1, SW1.2, TEST4.1, TH1.1, TH2.1, U4.6, U4.11, U4.19, U4.21, U4.22, U4.28, U4.50, U4.75, U4.100, U5.16, U6.12, U7.12, U8.12, U9.12, U12.1, X2.1
+5V: C29.1, C31.1, C33.1, C75.2, C76.2, L2.1, P17.2, R26.1, R65.2, TEST3.1, U12.11
+12V: C3.2, C21.2, C25.1, C27.1, C28.1, C30.1, C32.1, C54.2, C55.2, C72.2, C74.2, F2.2, L3.2, LS1.1, P11.1, P11.2, P11.3, P11.4, P12.1, P12.2, P12.3, P12.4, P13.1, P13.2, P13.3, P13.4, P14.1, P14.2, P14.3, P14.4, P15.1, P17.1, R5.2, R15.1, R18.1, R19.2, R66.2, TEST2.1, U1.4, U2.10, U3.4, U10.10, U11.10
+POWER: C2.1, C5.1, C6.1, C8.1, C9.1, D2.3, P1.1, Q1.3, R1.2, R6.2, R11.1, TEST1.1, U2.1, U6.1, U7.1, U8.1, U9.1
/Expansion I/O/ISO_IN_0: P21.5, U12.20
/Expansion I/O/ISO_IN_1: P21.4, U12.19
/Expansion I/O/ISO_IO_GND: C80.1, FB2.1, P21.8
/Expansion I/O/ISO_OUT_0: P21.9, U12.22
/Expansion I/O/ISO_OUT_1: P21.10, U12.21
/Output Circuits and Connectors/M1_PWR: P2.1, P2.3, U6.4
/Output Circuits and Connectors/M2_PWR: P3.1, P3.3, U7.4
/Output Circuits and Connectors/M3_PWR: P4.1, P4.3, U8.4
/Output Circuits and Connectors/M4_PWR: P5.1, P5.3, U9.4
AUX_ANALOG_0: D17.3, R48.5, U4.29
AUX_ANALOG_1: D18.3, R49.2, U4.30
AUX_PWM_0: D14.3, R48.8, U4.77
AUX_PWM_1: D15.3, R48.7, U4.53
AUX_PWM_2: D16.3, R48.6, U4.54
BOOT0: R28.1, SW1.1, U4.94
BOOT1: TEST8.1, U4.37
BUTTON_0: SW2.2, U4.7
BUTTON_1: SW3.2, U4.5
BUZZER_PWM: R62.2, U4.96
EXT_INPUT_0: U4.83, U12.5
EXT_INPUT_1: U4.81, U12.6
EXT_OUTPUT_0: U4.80, U12.3
EXT_OUTPUT_1: U4.82, U12.4
FAN_HALL: R29.1, U4.4
FAN_PWM: R60.2, U4.95
GND: C1.2, C2.2, C3.1, C4.1, C5.2, C6.2, C8.2, C9.2, C11.1, C12.1, C15.2, C16.2, C17.2, C18.2, C19.1, C20.1, C21.1, C25.2, C26.1, C27.2, C28.2, C30.2, C31.2, C32.2, C33.2, C34.2, C35.2, C36.2, C37.2, C38.2, C39.1, C40.2, C41.2, C42.2, C43.2, C44.2, C45.2, C46.2, C47.2, C48.2, C49.2, C50.1, C51.1, C52.1, C53.1, C54.1, C55.1, C56.1, C57.1, C58.1, C59.1, C60.2, C61.2, C62.2, C63.2, C64.2, C66.2, C67.2, C68.2, C69.2, C70.1, C71.1, C72.1, C73.1, C74.1, C75.1, C76.1, C77.1, D1.1, D4.C, D5.C, D6.1, D7.1, D8.1, D9.1, D10.A, D11.A, D12.A, D13.A, D14.1, D15.1, D16.1, D17.1, D18.1, D19.1, D20.1, D21.1, D22.1, D23.1, D24.C, MNT1.1, MNT2.1, MNT3.1, P1.2, P2.2, P2.4, P3.2, P3.4, P4.2, P4.4, P5.2, P5.4, P15.5, P16.6, P17.4, P17.5, P17.6, P19.1, P20.6, Q3.2, Q5.2, Q6.2, R3.1, R4.2, R7.1, R8.2, R10.2, R12.2, R14.2, R22.1, R23.1, R24.2, R25.2, R27.2, R28.2, R55.2, R58.2, R59.2, R61.2, R63.2, SW2.1, SW3.1, TEST5.1, U1.6, U1.EP, U2.6, U2.14, U2.EP, U3.6, U3.EP, U4.10, U4.20, U4.27, U4.74, U4.99, U5.9, U5.15, U6.5, U6.7, U6.8, U6.9, U6.10, U7.5, U7.7, U7.8, U7.9, U7.10, U8.5, U8.7, U8.8, U8.9, U8.10, U9.5, U9.7, U9.8, U9.9, U9.10, U10.9, U11.9, U12.2, U12.9, U12.10, U12.12, X1.2, X2.3, X2.5
I2C_SCK: D21.3, R34.2, R52.2, U4.47
I2C_SDA: D22.3, R33.1, R53.2, U4.48
ID_SPARE: P21.6, R32.2
ISOLATED_D+: P21.2, R68.1
ISOLATED_D-: P21.3, R67.1
ISOLATED_USB_GND: C22.1, C65.1, P21.1, U5.2, U5.8
ISOLATED_USB_VDD: C22.2, P21.7, U5.1
MOTOR_1_CURRENT: R35.5, U4.34
MOTOR_2_CURRENT: R35.6, U4.33
MOTOR_3_CURRENT: R35.7, U4.32
MOTOR_4_CURRENT: R35.8, U4.31
NRST: C38.1, U4.14, X2.10
unnamed: C1.1, D1.3, R2.1, R3.2, R57.4
unnamed: C4.2, U5.12, U5.13, U5.14
unnamed: C7.1, U1.3
unnamed: C7.2, L1.2, U1.5
unnamed: C10.1, R13.1, U2.9
unnamed: C10.2, C13.1, R14.1, R15.2, U2.8
unnamed: C11.2, U1.1, U1.9, U1.11, U1.12
unnamed: C12.2, D2.2, R11.2, R12.1, U2.2
unnamed: C13.2, R13.2
unnamed: C14.2, R9.2, R10.1, U1.10
unnamed: C16.1, U2.7
unnamed: C18.1, R16.2, U2.5
unnamed: C19.2, D3.1, R16.1, U2.16
unnamed: C20.2, R18.2, U2.17
unnamed: C23.1, L3.1, Q1.2, Q2.3, R20.1, U2.20
unnamed: C23.2, D3.3, R17.2
unnamed: C24.1, U3.3
unnamed: C24.2, L2.2, U3.5
unnamed: C26.2, U3.1, U3.9, U3.11, U3.12
unnamed: C29.2, R26.2, R27.1, U3.10
unnamed: C34.1, U4.49
unnamed: C36.1, U4.73
unnamed: C48.1, U4.8, X3.1
unnamed: C49.1, U4.9, X3.2
unnamed: C56.2, D10.C, R40.1, R44.2
unnamed: C57.2, D12.C, R42.1, R46.2
unnamed: C58.2, D11.C, R41.1, R45.2
unnamed: C59.2, D13.C, R43.1, R47.2
unnamed: C60.1, P15.2, R48.1
unnamed: C61.1, P15.3, R48.2
unnamed: C62.1, P15.4, R48.3
unnamed: C63.1, P15.7, R48.4
unnamed: C64.1, P15.8, R49.1
unnamed: C65.2, U5.3, U5.4, U5.5
unnamed: C66.1, P16.2, R50.1
unnamed: C67.1, P16.3, R51.1
unnamed: C68.1, P16.4, R52.1
unnamed: C69.1, P16.5, R53.1
unnamed: C70.2, R4.1, R57.1, TH1.2
unnamed: C71.2, R57.2, R58.1, TH2.2
unnamed: C73.2, P18.2, R57.3, R59.1
unnamed: C78.1, C79.1, FB2.2, R70.1, U12.13, U12.16, U12.23
unnamed: C78.2, C80.2, FB1.1, R69.1, U12.24
unnamed: C79.2, FB1.2, U12.14
unnamed: D4.A, R29.6
unnamed: D5.A, R29.5
unnamed: D23.3, R29.8, R61.1, R64.2
unnamed: D24.A, R29.7
unnamed: F1.1, P20.1
unnamed: F1.2, Q4.2
unnamed: F2.1, P19.2
unnamed: LS1.2, Q6.3
unnamed: P11.5, R44.1
unnamed: P11.6, U10.11
unnamed: P11.7, U10.12
unnamed: P11.8, U10.13
unnamed: P12.5, R45.1
unnamed: P12.6, U10.16
unnamed: P12.7, U10.17
unnamed: P12.8, U10.18
unnamed: P13.5, R46.1
unnamed: P13.6, U11.11
unnamed: P13.7, U11.12
unnamed: P13.8, U11.13
unnamed: P14.5, R47.1
unnamed: P14.6, U11.16
unnamed: P14.7, U11.17
unnamed: P14.8, U11.18
unnamed: P19.3, R64.1, R66.1
unnamed: P19.4, Q5.3, R65.1
unnamed: Q1.1, U2.19
unnamed: Q2.1, U2.15
unnamed: Q2.2, R21.1, R24.1
unnamed: Q3.1, R54.1, R55.1
unnamed: Q3.3, Q4.1, R56.2
unnamed: Q5.1, R60.1
unnamed: Q6.1, R62.1, R63.1
unnamed: R1.1, R2.2
unnamed: R5.1, U1.7
unnamed: R6.1, U2.4
unnamed: R7.2, U2.3
unnamed: R8.1, U1.2
unnamed: R17.1, U2.18
unnamed: R19.1, U3.7
unnamed: R20.2, R21.2, U2.12
unnamed: R22.2, U2.13
unnamed: R23.2, U2.11
unnamed: R25.1, U3.2
unnamed: R30.1, U5.11
unnamed: R31.1, U5.10
unnamed: R35.1, U9.11
unnamed: R35.2, U8.11
unnamed: R35.3, U7.11
unnamed: R35.4, U6.11
unnamed: R67.2, U5.6
unnamed: R68.2, U5.7
unnamed: R69.2, R70.2, U12.15
unnamed: U4.12, X1.1
unnamed: U4.13, X1.3
SERVO1_A: U4.65, U10.7
SERVO1_B: U4.66, U10.8
SERVO1_EN: U4.64, U10.6
SERVO1_HLFB: D6.3, R40.2, U4.63
SERVO2_A: U4.61, U10.2
SERVO2_B: U4.62, U10.3
SERVO2_EN: U4.60, U10.1
SERVO2_HLFB: D8.3, R41.2, U4.59
SERVO3_A: U4.44, U11.7
SERVO3_B: U4.45, U11.8
SERVO3_EN: U4.43, U11.6
SERVO3_HLFB: D7.3, R42.2, U4.40
SERVO4_A: U4.25, U11.2
SERVO4_B: U4.26, U11.3
SERVO4_EN: U4.24, U11.1
SERVO4_HLFB: D9.3, R43.2, U4.23
STATUS_0: R29.2, U4.3
STATUS_1: R29.3, U4.2
STATUS_2: R29.4, U4.1
SWCLK: U4.76, X2.4
SWDIO: U4.72, X2.2
SWO: U4.89, X2.6
TEMP_EXT_0: R57.7, U4.16
TEMP_EXT_1: R57.6, U4.17
TEMP_PCB: R57.8, U4.15
USART_1_RX: D20.3, R51.2, U4.93
USART_1_TX: D19.3, R50.2, U4.92
USART_2_CTS: P20.2, U4.84
USART_2_PWR_EN: R54.2, U4.88
USART_2_RTS: P20.3, U4.85
USART_2_RX: P20.5, U4.87
USART_2_TX: P20.4, U4.86
USB_D+: R31.2, U4.71
USB_D-: R30.2, U4.70
USB_OTG_ID: R32.1, U4.69
USB_VBUS: TEST6.1, U4.68
VOLTAGE_INPUT: R57.5, U4.18
~MOTOR_1_OC: R36.1, U4.58, U6.6
~MOTOR_2_OC: R37.1, U4.57, U7.6
~MOTOR_3_OC: R38.1, U4.36, U8.6
~MOTOR_4_OC: R39.1, U4.35, U9.6

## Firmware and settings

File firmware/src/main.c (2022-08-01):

/* Includes ------------------------------------------------------------------*/
#include "main.h"

#include "stm32f4xx_ll_bus.h"
#include "stm32f4xx_ll_pwr.h"
#include "stm32f4xx_ll_rcc.h"
#include "stm32f4xx_ll_system.h"
#include "stm32f4xx_ll_utils.h"

#include "app_hardware.h"
#include "app_tasks.h"
#include "global.h"
#include "hal_delay.h"
#include "hal_reset.h"
#include "hal_system_speed.h"
#include "hal_watchdog.h"
#include "qassert.h"
#include "status.h"

/* Private variables ---------------------------------------------------------*/
#if defined( NASSERT ) || defined( NDEBUG )
#if defined( USE_FULL_ASSERT ) || ( USE_FULL_ASSERT > 0 )
#error "You are building a RELEASE version while STM HAL library ASSERTs are still enabled!"
#endif
#endif

/* Private function prototypes -----------------------------------------------*/
void init_core( void );
void system_clock_config( void );

/* Private function prototypes -----------------------------------------------*/

//application entry point from startup_stm32f429xx.s
int main( void )
{
    init_core();              //Reset peripherals, init flash etc
    system_clock_config();    // Clocks

    app_hardware_init();    //Initialise IO, peripherals etc
    app_tasks_init();       //start the task handler

    //allow interrupts
    PERMIT();

#pragma clang diagnostic ignored "-Wmissing-noreturn"
    while( 1 )
    {
        if( !app_tasks_run() )
        {
            status_red( false );
            hal_watchdog_refresh();
            hal_system_speed_sleep();
        }
        hal_watchdog_refresh();
        status_red( true );
    }
}

void init_core( void )
{
    LL_FLASH_EnableInstCache();
    LL_FLASH_EnableDataCache();
    LL_FLASH_EnablePrefetch();

    LL_APB2_GRP1_EnableClock( LL_APB2_GRP1_PERIPH_SYSCFG );
    LL_APB1_GRP1_EnableClock( LL_APB1_GRP1_PERIPH_PWR );

    NVIC_SetPriorityGrouping( NVIC_PRIORITYGROUP_4 );

    // MemoryManagement_IRQn interrupt configuration
    NVIC_SetPriority( MemoryManagement_IRQn, NVIC_EncodePriority( NVIC_GetPriorityGrouping(), 0, 0 ) );

    // BusFault_IRQn interrupt configuration
    NVIC_SetPriority( BusFault_IRQn, NVIC_EncodePriority( NVIC_GetPriorityGrouping(), 0, 0 ) );

    // UsageFault_IRQn interrupt configuration
    NVIC_SetPriority( UsageFault_IRQn, NVIC_EncodePriority( NVIC_GetPriorityGrouping(), 0, 0 ) );

    // SVCall_IRQn interrupt configuration
    NVIC_SetPriority( SVCall_IRQn, NVIC_EncodePriority( NVIC_GetPriorityGrouping(), 0, 0 ) );

    // DebugMonitor_IRQn interrupt configuration
    NVIC_SetPriority( DebugMonitor_IRQn, NVIC_EncodePriority( NVIC_GetPriorityGrouping(), 0, 0 ) );

    // PendSV_IRQn interrupt configuration
    NVIC_SetPriority( PendSV_IRQn, NVIC_EncodePriority( NVIC_GetPriorityGrouping(), 0, 0 ) );

    // SysTick_IRQn interrupt configuration
    NVIC_SetPriority( SysTick_IRQn, NVIC_EncodePriority( NVIC_GetPriorityGrouping(), 0, 0 ) );
}

// Startup the internal and external clocks, set PLL etc
void system_clock_config( void )
{
    LL_FLASH_SetLatency( LL_FLASH_LATENCY_5 );

    if( LL_FLASH_GetLatency() != LL_FLASH_LATENCY_5 )
    {
        Error_Handler();
    }

    LL_PWR_SetRegulVoltageScaling( LL_PWR_REGU_VOLTAGE_SCALE1 );
    LL_PWR_DisableOverDriveMode();
    LL_RCC_HSE_Enable();

    while( LL_RCC_HSE_IsReady() != 1 )
    {
    }
    LL_RCC_LSI_Enable();

    while( LL_RCC_LSI_IsReady() != 1 )
    {
    }

    LL_RCC_PLL_ConfigDomain_SYS( LL_RCC_PLLSOURCE_HSE, LL_RCC_PLLM_DIV_4, 168, LL_RCC_PLLP_DIV_2 );
    LL_RCC_PLL_Enable();

    while( LL_RCC_PLL_IsReady() != 1 )
    {
    }

    LL_RCC_SetAHBPrescaler( LL_RCC_SYSCLK_DIV_1 );
    LL_RCC_SetAPB1Prescaler( LL_RCC_APB1_DIV_4 );
    LL_RCC_SetAPB2Prescaler( LL_RCC_APB2_DIV_4 );
    LL_RCC_SetSysClkSource( LL_RCC_SYS_CLKSOURCE_PLL );

    while( LL_RCC_GetSysClkSource() != LL_RCC_SYS_CLKSOURCE_STATUS_PLL )
    {
    }

    LL_Init1msTick( 168000000 );
    LL_SetSystemCoreClock( 168000000 );
    LL_RCC_SetTIMPrescaler( LL_RCC_TIM_PRESCALER_TWICE );
}

void onAssert__( const char *file,
                 unsigned    line,
                 const char *fmt,
                 ... )
{
    va_list  args;

    // Forward directly to the 'in-memory cache' handler function
    va_start( args, fmt );
    hal_reset_assert_cache( file, line, fmt, args );
    va_end( args );

    // Blinking lights while we wait for the watch dog to bite
    status_red( true );
    status_yellow( true );
    status_green( false );

    while( 1 )
    {
        hal_delay_ms( 100 );
        status_red_toggle();
        status_green_toggle();
    }
}

void _Error_Handler( char *file, int line )
{
    while( 1 )
    {
    }
}

#ifdef USE_FULL_ASSERT
void assert_failed( uint8_t *file, uint32_t line )
{
    // TODO: implement full assert handler
}
#endif /* USE_FULL_ASSERT */

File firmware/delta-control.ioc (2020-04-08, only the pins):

Mcu.UserName=STM32F429VETx
PA0/WKUP.GPIO_Label=SERVO_4_HLFB
PA0/WKUP.Signal=S_TIM5_CH1
PA1.GPIO_Label=SERVO_4_ENABLE
PA1.Signal=GPIO_Output
PA10.Signal=USB_OTG_FS_ID
PA13.Signal=SYS_JTMS-SWDIO
PA14.Signal=SYS_JTCK-SWCLK
PA15.GPIO_Label=AUX_PWM_0
PA15.Signal=S_TIM2_CH1_ETR
PA2.GPIO_Label=SERVO_4_A
PA2.Signal=S_TIM5_CH3
PA3.GPIO_Label=SERVO_4_B
PA3.Signal=S_TIM5_CH4
PA4.GPIO_Label=AUX_ANALOG_0
PA4.Signal=COMP_DAC1_group
PA5.GPIO_Label=AUX_ANALOG_1
PA5.Signal=COMP_DAC2_group
PA6.GPIO_Label=MOTOR_4_CURRENT
PA6.Signal=ADCx_IN6
PA7.GPIO_Label=MOTOR_3_CURRENT
PA7.Signal=ADCx_IN7
PA9.Signal=USB_OTG_FS_VBUS
PB0.GPIO_Label=MOTOR_4_OC
PB0.Signal=GPIO_Input
PB1.GPIO_Label=MOTOR_3_OC
PB1.Signal=GPIO_Input
PB10.GPIO_Label=AUX_SCL
PB10.Signal=I2C2_SCL
PB11.GPIO_Label=AUX_SDA
PB11.Signal=I2C2_SDA
PB14.GPIO_Label=EXT_PWM_2
PB14.Signal=S_TIM12_CH1
PB15.GPIO_Label=EXT_PWM_1
PB15.Signal=S_TIM12_CH2
PB3.Signal=SYS_JTDO-SWO
PB6.GPIO_Label=AUX_TX
PB6.Signal=USART1_TX
PB7.GPIO_Label=AUX_RX
PB7.Signal=USART1_RX
PB8.GPIO_Label=FAN_PWM
PB8.Signal=S_TIM10_CH1
PB9.GPIO_Label=BUZZER_PWM
PB9.Signal=S_TIM11_CH1
PC0.GPIO_Label=TEMP_PCB
PC0.Signal=ADCx_IN10
PC1.GPIO_Label=TEMP_EXT_0
PC1.Signal=ADCx_IN11
PC12.GPIO_Label=EXT_OUTPUT_0
PC12.Signal=UART5_TX
PC13.GPIO_Label=BUTTON_0
PC13.Signal=GPIO_Input
PC14/OSC32_IN.Signal=RCC_OSC32_IN
PC15/OSC32_OUT.Signal=RCC_OSC32_OUT
PC2.GPIO_Label=TEMP_EXT_1
PC2.Signal=ADCx_IN12
PC3.GPIO_Label=V_SENSE
PC3.Signal=ADCx_IN13
PC4.GPIO_Label=MOTOR_2_CURRENT
PC4.Signal=ADCx_IN14
PC5.GPIO_Label=MOTOR_1_CURRENT
PC5.Signal=ADCx_IN15
PC6.GPIO_Label=SERVO_1_HLFB
PC6.Signal=S_TIM3_CH1
PC7.GPIO_Label=SERVO_1_ENABLE
PC7.Signal=GPIO_Output
PC8.GPIO_Label=SERVO_1_A
PC8.Signal=S_TIM3_CH3
PC9.GPIO_Label=SERVO_1_B
PC9.Signal=S_TIM3_CH4
PD0.GPIO_Label=EXT_INPUT_1
PD0.Signal=CAN1_RX
PD1.GPIO_Label=EXT_OUTPUT_1
PD1.Signal=CAN1_TX
PD10.GPIO_Label=MOTOR_2_OC
PD10.Signal=GPIO_Input
PD11.GPIO_Label=MOTOR_1_OC
PD11.Signal=GPIO_Input
PD12.GPIO_Label=SERVO_2_HLFB
PD12.Signal=S_TIM4_CH1
PD13.GPIO_Label=SERVO_2_ENABLE
PD13.Signal=GPIO_Output
PD14.GPIO_Label=SERVO_2_A
PD14.Signal=S_TIM4_CH3
PD15.GPIO_Label=SERVO_2_B
PD15.Signal=S_TIM4_CH4
PD2.GPIO_Label=EXT_INPUT_0
PD2.Signal=UART5_RX
PD3.GPIO_Label=MODULE_CTS
PD3.Signal=USART2_CTS
PD4.GPIO_Label=MODULE_RTS
PD4.Signal=USART2_RTS
PD5.GPIO_Label=MODULE_TX
PD5.Signal=USART2_TX
PD6.GPIO_Label=MODULE_RX
PD6.Signal=USART2_RX
PD7.GPIO_Label=MODULE_PWR_EN
PD7.Signal=GPIO_Output
PE12.GPIO_Label=SERVO_3_ENABLE
PE12.Signal=GPIO_Output
PE13.GPIO_Label=SERVO_3_A
PE13.Signal=S_TIM1_CH3
PE14.GPIO_Label=SERVO_3_B
PE14.Signal=S_TIM1_CH4
PE2.GPIO_Label=STATUS_2
PE2.Signal=GPIO_Output
PE3.GPIO_Label=STATUS_1
PE3.Signal=GPIO_Output
PE4.GPIO_Label=STATUS_0
PE4.Signal=GPIO_Output
PE5.GPIO_Label=FAN_TACH
PE5.Signal=S_TIM9_CH1
PE6.GPIO_Label=BUTTON_1
PE6.Signal=GPIO_Input
PE9.GPIO_Label=SERVO_3_HLFB
PE9.Signal=S_TIM1_CH1
PH0/OSC_IN.Signal=RCC_OSC_IN
PH1/OSC_OUT.Signal=RCC_OSC_OUT

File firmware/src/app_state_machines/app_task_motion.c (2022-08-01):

/* ----- System Includes ---------------------------------------------------- */

#include <event_subscribe.h>
#include <string.h>

/* ----- Local Includes ----------------------------------------------------- */
#include "app_config.h"
#include "app_events.h"
#include "app_signals.h"
#include "app_times.h"
#include "qassert.h"

#include "app_task_motion.h"

#include "clearpath.h"
#include "kinematics.h"
#include "motion_types.h"
#include "path_interpolator.h"

#include "user_interface.h"

DEFINE_THIS_FILE; /* Used for ASSERT checks to define __FILE__ only once */

/* ----- Private Function Definitions --------------------------------------- */

PRIVATE void AppTaskMotionConstructor( AppTaskMotion *me );

PRIVATE void  AppTaskMotion_initial( AppTaskMotion *me, const StateEvent *e );
PRIVATE STATE AppTaskMotion_main( AppTaskMotion *me, const StateEvent *e );
PRIVATE STATE AppTaskMotion_home( AppTaskMotion *me, const StateEvent *e );
PRIVATE STATE AppTaskMotion_inactive( AppTaskMotion *me, const StateEvent *e );
PRIVATE STATE AppTaskMotion_active( AppTaskMotion *me, const StateEvent *e );
PRIVATE STATE AppTaskMotion_recovery( AppTaskMotion *me, const StateEvent *e );

PRIVATE void AppTaskMotion_commit_queued_move( AppTaskMotion *me );
PRIVATE void AppTaskMotion_clear_queue( AppTaskMotion *me );
PRIVATE void AppTaskMotion_add_event_to_queue( AppTaskMotion *me, const StateEvent *e );

typedef enum
{
    TASKSTATE_MOTION_INITIAL = 0,
    TASKSTATE_MOTION_MAIN,
    TASKSTATE_MOTION_HOME,
    TASKSTATE_MOTION_INACTIVE,
    TASKSTATE_MOTION_ACTIVE,
    TASKSTATE_MOTION_RECOVERY,
} MotionTaskState_t;

/* ----- Public Functions --------------------------------------------------- */

PUBLIC StateTask *
appTaskMotionCreate( AppTaskMotion *me,
                     StateEvent    *eventQueueData[],
                     const uint8_t  eventQueueSize,
                     StateEvent    *movementQueue[],
                     const uint8_t  movementQueueSize )
{
    // Clear all task data
    memset( me, 0, sizeof( AppTaskMotion ) );

    // Initialise State Machine State
    AppTaskMotionConstructor( me );

    /* Initialise State Machine Task */
    return stateTaskCreate( (StateTask *)me,
                            eventQueueData,
                            eventQueueSize,
                            movementQueue,
                            movementQueueSize );
}

/* ----- Private Functions -------------------------------------------------- */

// State Machine Construction
PRIVATE void AppTaskMotionConstructor( AppTaskMotion *me )
{
    stateTaskCtor( &me->super, (State)&AppTaskMotion_initial );
}

/* -------------------------------------------------------------------------- */

// State Machine Initial State
PRIVATE void AppTaskMotion_initial( AppTaskMotion *me, const StateEvent *e __attribute__( ( __unused__ ) ) )
{
    eventSubscribe( (StateTask *)me, MOTION_PREPARE );
    eventSubscribe( (StateTask *)me, MOTION_EMERGENCY );

    eventSubscribe( (StateTask *)me, MOTION_QUEUE_ADD );
    eventSubscribe( (StateTask *)me, MOTION_QUEUE_CLEAR );
    eventSubscribe( (StateTask *)me, MOTION_QUEUE_START );

    eventSubscribe( (StateTask *)me, PATHING_COMPLETE );

    kinematics_init();
    path_interpolator_init();
    user_interface_set_motion_state( TASKSTATE_MOTION_INITIAL );

    STATE_INIT( &AppTaskMotion_main );
}

/* -------------------------------------------------------------------------- */

PRIVATE STATE AppTaskMotion_main( AppTaskMotion *me, const StateEvent *e )
{
    switch( e->signal )
    {
        case STATE_ENTRY_SIGNAL:
            user_interface_set_motion_state( TASKSTATE_MOTION_MAIN );

            return 0;

        case MOTION_PREPARE:
            STATE_TRAN( AppTaskMotion_home );
            return 0;

        case MOTION_EMERGENCY:
            STATE_TRAN( AppTaskMotion_recovery );
            return 0;
    }
    return (STATE)hsmTop;
}

/* -------------------------------------------------------------------------- */

PRIVATE STATE AppTaskMotion_home( AppTaskMotion *me, const StateEvent *e )
{
    switch( e->signal )
    {
        case STATE_ENTRY_SIGNAL:

            me->retries = 0;

            // Reset the motors and let them home
            for( ClearpathServoInstance_t servo = _CLEARPATH_1; servo < _NUMBER_CLEARPATH_SERVOS; servo++ )
            {
                servo_start( servo );
            }

            user_interface_set_motion_state( TASKSTATE_MOTION_HOME );

            // Check the motors every 500ms to see if they are homed
            eventTimerStartEvery( &me->timer1,
                                  (StateTask *)me,
                                  (StateEvent *)&stateEventReserved[STATE_TIMEOUT1_SIGNAL],
                                  MS_TO_TICKS( SERVO_HOMING_SUPERVISOR_CHECK_MS ) );

            return 0;

        case STATE_TIMEOUT1_SIGNAL:

            // Check all the servos have homed successfully by polling their manager for a 'all good' condition
            me->counter = 0;
            for( ClearpathServoInstance_t servo = _CLEARPATH_1; servo < _NUMBER_CLEARPATH_SERVOS; servo++ )
            {
                me->counter += servo_get_servo_ok( servo );

                // The servo is/recently entered an error recovery state
                if( servo_get_servo_did_error( servo ) )
                {
                    // Bail out of the mechanism homing process entirely
                    // while catching the error and re-requesting the servo to home would be nice, we let the user do that
                    eventPublish( EVENT_NEW( StateEvent, MOTION_ERROR ) );
                    STATE_TRAN( AppTaskMotion_recovery );
                }
            }

            if( me->counter == SERVO_COUNT )
            {
                eventPublish( EVENT_NEW( StateEvent, MOTION_HOMED ) );
                path_interpolator_set_home();
                STATE_TRAN( AppTaskMotion_inactive );
            }
            else
            {
                // Allow subsequent homing check retries
                if( me->retries++ > SERVO_HOMING_SUPERVISOR_RETRIES )
                {
                    eventPublish( EVENT_NEW( StateEvent, MOTION_ERROR ) );
                    STATE_TRAN( AppTaskMotion_recovery );
                }
            }

            return 0;

        case MOTION_QUEUE_ADD:
            AppTaskMotion_add_event_to_queue( me, e );
            return 0;

        case MOTION_EMERGENCY:
            STATE_TRAN( AppTaskMotion_recovery );
            return 0;

        case STATE_EXIT_SIGNAL:
            eventTimerStopIfActive( &me->timer1 );

            return 0;
    }
    return (STATE)hsmTop;
}

/* -------------------------------------------------------------------------- */
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

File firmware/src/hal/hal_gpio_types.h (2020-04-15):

#ifndef HAL_GPIO_TYPES_H
#define HAL_GPIO_TYPES_H

#ifdef __cplusplus
extern "C" {
#endif

/* ----- System Includes ---------------------------------------------------- */

/* ----- Local Includes ----------------------------------------------------- */

#include "global.h"

/* ----- Defines ------------------------------------------------------------ */

/** Readability macros to remind us which is a HIGH level or LOW level */
#define GPIO_HIGH true
#define GPIO_LOW  false

/** Map the pin number into a bit mask */
#define HAL_GPIO_PIN_MASK( pin_nr ) ( ( uint16_t )( 1U << ( pin_nr ) ) )

/** Port Number */
typedef enum
{
    PORT_A = ( 0 ),
    PORT_B = ( 1 ),
    PORT_C = ( 2 ),
    PORT_D = ( 3 ),
    PORT_E = ( 4 ),
    PORT_F = ( 5 ),
    PORT_G = ( 6 ),
    PORT_H = ( 7 ),
    PORT_I = ( 8 ),
    PORT_J = ( 9 ),
    PORT_K = ( 10 ),
} HalGpioPortNr_t;

/** Pin Numbers */
typedef enum
{
    PIN_0,
    PIN_1,
    PIN_2,
    PIN_3,
    PIN_4,
    PIN_5,
    PIN_6,
    PIN_7,
    PIN_8,
    PIN_9,
    PIN_10,
    PIN_11,
    PIN_12,
    PIN_13,
    PIN_14,
    PIN_15,
} HalGpioPinNr_t;

typedef struct
{
    unsigned mode    : 3;      /* GPIO Mode (Analog, Input, Output Push Pull, etc. ) */
    unsigned port    : 4;      /* GPIO Port */
    unsigned pin     : 5;      /* Pin Number within port */
    unsigned initial : 1;      /* Initialisation level for outputs */
} HalGpioDef_t;

/* ----- End ---------------------------------------------------------------- */

#ifdef __cplusplus
}
#endif

#endif /* HAL_GPIO_TYPES_H */

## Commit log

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2018-03-20 Clearances, shelled end effector, misc
    [arm_clevis_assembly.SLDASM, arm_mech_assembly.SLDASM, bearing_link.SLDPRT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]
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2018-03-25 Resolved supressed end effector part
    [arm_mech_assembly.SLDASM, effector_assembly.SLDASM, effector_planar.SLDPRT]
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2018-03-28 Updates to clevis and assemblies
    End affector uses more sane distances to pivot.
    Clevis interference resolved.
    General cleanup and fixes
    [arm_clevis_assembly.SLDASM, arm_mech_assembly.SLDASM, bearing_link_assembly.SLDASM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]
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2018-04-02 Micro pinout and stubs on exp sheets
    Other cleanup and fixes.
    Slowly fleshing out content.
    [expansion_io.sch, microcontroller.sch, motor_outputs.sch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]
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2018-04-03 Rework of bicep design
    Uses 'I-Beam' style instead of truss
    [bicep.SLDPRT, bicep_assembly.SLDASM, bicep_elbow.SLDPRT]
2018-04-03 Updated/reworked end effector geometry
    Rework for correct spacing, offsets, bearing spacers, etc.
    [arm_mech_assembly.SLDASM, effector_assembly.SLDASM, effector_planar.SLDPRT]
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2018-04-08 Update of master assembly, started weight reduction on topplate
    Cutouts on internal face, other tweaks and fixes as appropriate
    [base_plate.SLDPRT, bottom_plate_detail.SLDPRT, effector_assembly.SLDASM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]
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2018-04-09 Updated tolerances on side plates
    [side_cover_fan.SLDPRT, side_cover_full.SLDPRT, side_cover_vent.SLDPRT]
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2018-04-13 Drawing updates and fixes
    Tolerance tweaks, misc.
    [base_plate_light.SLDDRW, base_plate_light.STEP, base_plate_simple.SLDDRW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]
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2018-04-17 Minor cleanup
    USB ID wiring, fixed floating power object in motor page, etc
    [microcontroller.sch, motor_outputs.sch, power.sch]
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2018-04-18 Symbol replacements and general cleanup
    Correct ULN2803A symbol/fp.
    Cleanup of test hooks, text labels, positions, connectors, etc.
    [expansion_io.sch, motor_outputs.sch, power.sch]
2018-04-18 Swapped to quad resistor arrays where practical.
    Shifted some test points and resistors to potentially simpify routing.
    General cleanup of aux area.
    [expansion_io.sch, microcontroller.sch, motor_outputs.sch]
2018-04-18 Annotation
    Minor part placement/fixes for quad array annotation ordering.
    Annotated and performed footprint association.
    [expansion_io.sch, microcontroller.sch, motor_outputs.sch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]
2018-04-19 Fixed incorrect footprint assignment on molex minifit connectors
    [motor_outputs.sch]
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2018-04-21 Routing and layout improvements
    Reworked some pinouts/connector assignments, part switching etc.
    [expansion_io.sch, microcontroller.sch, motor_outputs.sch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]
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2018-04-25 Added sch objects for the additional logo items, finished all routing
    Added symbols for HV, temp warning, connectors, etc.
    Most pours are now made, played with clearances and internal planes somewhat
    [zaphod-controller.kicad_pcb, zaphod-controller.sch]
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2018-04-26 Added buzzer, notes on pcb sheets
    Dimensions, stack info, etc.
    [expansion_io.sch, microcontroller.sch, power.sch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]
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2018-04-30 PCB updates and minor tweaks
    Based on review notes, few resistor changes, more stitching vias, increased clearances. Added polyfuse to add-in card module.
    Tightened up soldermask clearances, etc.
    [expansion_io.sch, zaphod-controller.kicad_pcb]
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2018-04-30 Generated Issue 1 manufacturing outputs, pdf, step
    [zaphod-controller-B.Cu.gbr, zaphod-controller-B.Fab.gbr, zaphod-controller-B.Mask.gbr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]
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2018-05-01 Reduced width of some pads to increase min-clearance to 0.2mm
    Was 0.17mm, fab complained about 75um copper and this clearance.
    Affects regulator IC, IO isolation device.
    [zaphod-controller-B.Cu.gbr, zaphod-controller-B.Fab.gbr, zaphod-controller-B.Mask.gbr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]
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2018-05-05 Rework of hal_pwm. Uses simplified init functions instead of cubeMX.
    Groups multiple timer configurations into groups based on usage requirement.
    Far easier to logically group/understand, and cleaner setup calls.
    Reworked hal_gpio to support alternative function pin init.
    Replaced all IO setup/destruction in hal_pwm with calls to hal_gpio to keep hal responsibilities clearer.
    [hal_gpio.c]
2018-05-05 Removed redundant includes in most of hal layer
    std_bool and std_int were included on most files, but are already included in global.
    This reduces import noise.
    [hal_adc.c, hal_gpio.c, hal_gpio_types.h]
2018-05-05 Added fan driver
    Simple statemachine to handle speed set/get with short 'blip' to ensure reliable starts.
    [app_background.c, app_hardware.c, fan.c]
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2018-05-06 Updated buzzer driver to use correct hal_pwm calls
    [buzzer.c]
2018-05-07 Fleshed out clearpath driver
    Mid layer driver to handle bit-banging the pulse train, handling homing, error handling for a single motor.
    Added instance of this driver for each motor for background processing etc.
    [app_background.c, app_hardware.c, clearpath.c]
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2018-05-12 Rate limit background tasks
    Button processing, fan speed updates, and buzzer handling don't need to run on every loop. Throttle them to more sensible rates .
    [app_background.c]
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2018-05-13 hal_uart cleanup and prep for correct ports. Minor tweaks to gpio AFinit
    hal_uart older code was replaced with the newer hal_gpio style of init/deconstruct as used in hal_pwm.
    Ports and bauds updated, cleanup.
    [hal_gpio.c]
2018-05-14 Clearpath driver clamps input angle to provide software endstops
    Prevents requested movements exceeding motion envelope of servos
    [clearpath.c]
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2018-05-20 Added stop function to clearpath driver
    Allows higher level handlers to request a stop/disable of the servo.
    Currently brute forces it through the failsafe states towards idle.
    [clearpath.c]
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2018-05-25 Minor changes to begin board bringup
    Fixed assert, changed fan temp probe to a PCB sensor, resistor value change on board temp sensor, debug configuration.
    [delta-control Debug.cfg]
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2018-05-26 Fixed ADC setup issues
    Readings now seem correct, and correctly aligned in buffer.
    [hal_adc.c]
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2018-05-26 Updated pwm calls in fan and buzzer driver, reduced fan temp check rate
    Fan-speed now evaluated every half second.
    [buzzer.c, fan.c]
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2018-06-03 Fixed incorrect labels for yellow and green LEDs
    Resolves issue where leds didn't seem to respond correctly...
    [status.c]
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2018-06-04 Fixed button's missing internal pullup setting.
    Buttons now work as intended.
    [hal_gpio.c]
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2018-06-09 Bug fixes in interpolator
    Actually exits idle mode when inbound movement calcs are required.
    Fixed incorrect percentage completion timer.
    [path_interpolator.c]
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2018-06-10 When counting successfully homed motors, only check 4th if enabled
    Otherwise a normal homing sequence fails without a 4th axis...
    [app_task_motion.c]
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2018-06-16 Minor cleanup of internal progname define and release/debug flags
    Correctly named program define.
    Added __DEBUG flag to debug configuration to allow correct auto generation of correct build name.
    PROG Build information is set in the set_defaults configuration function.
    Formatting improvements.
    [configuration.c]
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2018-06-16 Sensor driver publishes data to config handler
    Streamlines calls and ensures that the UI has access to the latest conversions.
    Makes it easier to clamp/error check sensors in future.
    [sensors.c]
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2018-06-16 Correctly init kinematics and pathing, refactor configuration setters
    [configuration.h]
2018-06-16 Tweaks and fixes in motion pipeline
    Breakpoint step validation from event generation through to motor controls.
    Most values/offsets etc seem reasonable at a glance, need either UI or hardware test to better validate correct operation.
    [app_task_supervisor.c, app_times.h, clearpath.c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]
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2018-06-18 Added settings for expansion (internal and external) IO settings
    Should allow the UI to communicate what periperals are used for expansions, and to expose runtime swaps to the UI
    [configuration.h]
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2018-07-01 Fan state (on/off/starting/stall) now published to configuration
    Stall state added (waits, adds speed if needed, restarts), publishes state.
    [configuration.h]
2018-07-01 Correctly handle build information in info structure
    [app_hardware.c, configuration.c]
2018-07-02 Servo information sent to configuration for display on UI
    Removed current, as power is the useful variable.
    Reports state, enabled, power info.
    Reports angle targets when inbound targets are set.
    Doesn't handle current angle yet.
    [configuration.h]
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2018-07-02 Fan hall reading cached for process function, reduces repeated calls
    Adds configuration output for UI display.
    Doesn't currently have a valid speed reading assigned.
    [fan.c]
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2018-07-03 Reduced obsolete forced ADC polling for UI, fixed incorrect hwNum define
    Hardware number is 1 for the first revision. A 0th revision PCB isn't possible?
    Was double polling/setting ADC values to configuration handler.
    Fixed button poll time being too sparse to catch press events.
    [app_background.c, app_times.h]
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2018-07-08 Fixed homing issue and direction swap in clearpath driver
    Fixed issue where PWM feedback enum storage was used instead of pin in the pin read.
    Fixed issue where motor command was in opposite direction than intended.
    Fixed issue where valid home reporting required mid-homing valid flags (hold-over from conceptual PWM feedback code).
    Commented power fault monitoring as ADC readings haven't been stabilized/calibrated properly yet.
    [clearpath.c]
2018-07-09 Minor cleanup around clearpath and motion task
    Formatting fixes, motion task uses recovery when identifying faults instead of firing an event
    [app_background.c, app_task_motion.c, clearpath.c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]
2018-07-10 Added cartesian movement limits to pathing engine
    Prevents inbound movements from exceeding the xyz bounds.
    [path_interpolator.c]
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2018-07-11 Fixed potential pathing bugs in floating point percentage handling
    Uses the epsilon found in float.h and compares floats on eps ranges instead of the poorly thought out direct comparisons
    [path_interpolator.c]
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2018-07-11 UI data struct additions, movements from UI, cleanup
    General cleanup and fixes to flesh out UI state and progress indication.
    Accepts movement structure and 'add to queue' callback.
    Added hash/id field to movement object.
    [configuration.h]
2018-07-11 Fixed compile warning on UUID to eUI cast
    [app_tasks.c, configuration.c]
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2018-07-26 Tweaked servo idle high-load identification values and behaviour
    Adjusts idle state servo error check behaviour based on physical testing
    [app_times.h, clearpath.c]
2018-07-26 Motion task bug fixes to allow for motor restarts after e-stop
    When an estop or similar recovery state is used, we now return to an idle state and allow rehoming.
    [app_task_motion.c]
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2018-07-27 Clear the motion queue when a e-stop recovery is handled
    Prevents old motion items in the queue from running once the mechanism recovers from a forced stop/fault.
    [app_task_motion.c]
2018-07-28 Fixed hardcoded 3D step model paths in pcb cache
    Resolves issue where 3D models are against absolute paths on windows desktop kicad install
    [zaphod-controller.kicad_pcb]
2018-07-28 Added function to reset global position in Interpolator
    Allows supervisor to 'home' the global position state.
    [path_interpolator.c]
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2018-07-28 Minor formatting fixes
    Comments in a few files.
    Uses lifo instead of fifo for motion queue.
    Minor syntactical change on home reset function.
    [app_task_motion.c, app_times.h, path_interpolator.c]
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2018-07-29 Cleaned clearpath driver and fixed issue where old positions were held
    Fixes issue where previous position estimate was held after a fresh homing process, causing incorrect movements against the angle request.
    [clearpath.c, path_interpolator.c]
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2018-08-01 Fixed motion handler not running through accumulated queue movements
    Increased queue size to 50.
    Moved motion items to 'large' event pool type.
    Various flailings in motion handler to get queue state management to behave more intelligently.
    Seems to work pretty well with manually forced queues.
    [app_task_motion.c, app_tasks.c]
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2018-09-02 Added missing 6th forearm
    [arm_clevis_assembly.SLDASM, arm_mech_assembly.SLDASM, bearing_link_assembly.SLDASM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]
2018-09-02 Cosmetic improvements and tolerance pass of mechanism
    [CDG5-12.SLDASM, arm_clevis_assembly.SLDASM, bearing_link.SLDPRT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]
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2018-09-22 Path interpolator transit functionality added/fixed
    [path_interpolator.c]
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2018-09-29 Fleshing out supervisor state machine
    Shifting responsibilities upwards, reworking motion handler, additional data to configuration, etc.
    [configuration.h]
2018-09-29 Improve homing and error handling processes
    Closes a few corner-cases.
    Aligns real states with physical actions more closely.
    Better UI display of state information.
    [app_task_supervisor.c, clearpath.c, configuration.c]
2018-09-30 Better visibility of supervisor armed/transits/disarmed states with LED
    Onboard LEDs represent the arming states of the supervisor.
    Improved error recovery check process.
    [app_task_supervisor.c, app_times.h, clearpath.c]
2018-09-30 Fixed bugs where supervisor got caught in wrong state
    Resolves issues where external cause of mechansim failure wasn't kicking the supervisor out properly.
    Resolves issue where homing event wasn't being handled properly.
    [app_task_supervisor.c, configuration.c]
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2018-10-14 Controller behaviour roughly implemented, control mode change improved
    Now skips the movement to home if already there.
    Now tracks target position at 10hz.
    Added macro for range test.
    [app_task_supervisor.c, configuration.c]
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2018-12-28 Fixed issue with push-button arming immediately hitting failsafe
    Needed a specific mode set before arming, minor tweaks.
    [app_task_supervisor.c, app_times.h]
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2019-07-16 Fixed incorrect use of an additional eventpool
    There can only be three...
    [app_tasks.c]
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2019-07-18 Fixed issue where motion task would hang in active mode
    Resolves issue where new inbound moves wouldn't start, and a clear queue was needed to reset the motion task to inactive before triggering a sync start.
    [app_task_motion.c, app_task_supervisor.c, configuration.c]
2019-07-18 Fixed led task getting stranded when inbound id didn't require animation
    Resolves issue where the led handler would get stranded in the active mode when the motion task was processing moves with lower id's than the current led queue head.
    [app_task_led.c, app_task_supervisor.c]
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2019-08-03 Allow immediate execution of moves with id:0 for manual jog control
    Fixes regression to manual (and self-published moves for homing etc) mode requiring a 'start queue' event.
    [app_task_motion.c, app_task_supervisor.c, configuration.c]
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2019-08-11 Fixed bug in path_interpolator where invalid target location is returned
    Incorrect value/pointer copy bug which caused 0,0,0 target to be used when at end of the range, regardless of validity
    [path_interpolator.c]
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2019-08-21 Publish error messages to the UI
    [configuration.h]
2019-08-21 Fixed bug where incomplete mode change would leave mechanism at not-home
    Supervisor retries homing moves, rather than assuming the first worked.
    [app_task_supervisor.c]
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2019-08-21 Reset path_interpolator, clearpath error event to improve error handling
    [configuration.h]
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2019-08-23 Fixed firmware bug where peeking from led queue grabbed invalids
    [app_task_led.c, app_task_motion.c]
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2019-08-29 Automatically add motion requests to queue, fixed tracked move deadband
    [app_task_supervisor.c, configuration.c]
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2019-08-30 Pathing engine makes copy of inbound move instead of pointer
    Resolves issue where repeated moves in manual mode would override each other, rather than queue properly.
    [path_interpolator.c]
2019-08-30 Event driven tracked positioning rework
    Event driven rather than polled target position, calculates move to achieve constant speed tracking
    [app_task_motion.c, app_task_supervisor.c, path_interpolator.c]
2019-08-30 Tracked mode cancels current movement if new one comes in
    Allows direction reversal while a longer move was being executed.
    [app_task_motion.c, app_task_supervisor.c, path_interpolator.c]
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2019-10-09 Probably fixed issues with LED offsets
    [led.c]
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2019-10-11 Fixed unresponsive home action behaviour while in event mode
    [app_task_supervisor.c]
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2019-11-08 Minor firmware refactor, spelling fixes
    [app_background.c, app_task_motion.c, app_times.h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]
2019-11-08 LED Task queue handling improvements - fixes missing ID sync behaviour
    [app_task_led.c]
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2019-11-11 Motion task - removed ID reporting, reworked active mode
    Previous functionality required the motion handler to drop to idle mode to report the movement ID, allowing the supervisor to fire a barrier event with the next ID.
    Active mode now supports both slots in the pathing interpolator.
    [app_task_motion.c, app_task_supervisor.c, path_interpolator.c]
2019-11-11 Motion task - fixed homing bugs introduced during refactor
    [app_task_motion.c, app_task_supervisor.c, path_interpolator.c]
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2019-11-11 LED task and interpolator rework started
    [app_task_led.c, path_interpolator.c]
2019-11-11 LED Interpolator dual-animation ping-pong buffer for reduced latency
    Allows immediate swaps to the next preloaded lighting event.
    [path_interpolator.c]
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2019-11-11 Fixed relative move behaviour after ping-pong refactor
    Refactor meant that calculating the absolute version of a relative move when it's added to the pathing engine wasn't using the right position, as the pathing engine was actually executing another move, and using the instantaneous effector position as the absolute move base.
    [path_interpolator.c]
2019-11-11 Fixed bug where last Led task became inactive too early
    [app_task_led.c, path_interpolator.c]
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2019-11-13 Servo homing angle cleanup fixes first-move jerk after arming
    [clearpath.c]
2019-11-24 Reverted harmonic drive concepts from CAD
    [40¢╗▓µ.sldprt, 40Íß│ð.sldprt, XB1-AS-GF-40-D8.SLDASM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]
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2019-12-30 Fixed fan PWM output issues
    Output PWM signal was inverted, regression likely due to refactor of PWM set functions during LED integration.
    [configuration.h]
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2020-01-01 Hardware Input Capture driver fleshed out/fixed
    Fixed issue where HALL sensor wasn't being sampled properly.
    Started building out driver functionality.
    [main.c]
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2020-01-02 Disable WakeUP Pin, comment fixes, adds MODE_AF_OD to gpio enum
    [clearpath.c, hal_gpio.c]
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2020-01-04 Adds resistor across buzzer to 'pullup' the low side.
    This is why the buzzer wouldn't make noise. Sch note added to fix oversight.
    [expansion_io.sch]
2020-01-04 Supervisor generates tones to indicate arming/ok/error and mode change
    [app_task_supervisor.c, app_times.h]
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2020-01-07 Correct units for calibration voltages/current values
    [sensors.c]
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2020-01-18 Buzzer beeps when saving or wiping persistent settings
    [configuration.c]
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2020-04-08 Fixed USART bug, added vendor LL libs to repo
    [app_tasks.c, hal_gpio.c]
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2020-04-08 Sweeping refactor and fixes
    [app_background.c, app_tasks.c]
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2020-04-08 Fixed CCRAM linker behaviour
    Correctly put the large event buffer in CCRAM, without duplication in FLASH.
    [app_tasks.c]
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2020-04-13 Fixed fw bug: handshakes with UI while armed causes events to fire
    [app_times.h, configuration.c]
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2020-04-14 Microcontroller queries reset register for power-up cause, shows in UI
    [configuration.h]
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2020-04-15 Formatting consistency fixes
    Sweeping enforcement of clang-format styles
    [configuration.h]
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2020-04-17 Minor cleanup/fixes of pathing engine logic
    [app_task_motion.c, path_interpolator.c]
2020-04-18 Cleanup and fixes around tracked position mode
    Crude velocity damping on tracked position targets reduces jerk on move starts etc
    [app_task_supervisor.c]
2020-04-18 Handle servo error and recovery more graciously during homing
    Better handling of servo shutdown and servo homing, reduced unnecessary delays in servo 'shutdown wait' and made higher level motion handler states more responsive to errors.
    [app_task_motion.c, app_task_supervisor.c, app_times.h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]
2020-04-19 Fixed missed formatting on fw main.c
    [main.c]
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2022-08-01 Fix formatting/orders of MSGID enum/defines
    with some minor refactor.
    [user_interface.c, user_interface_msgid.h]
2022-08-01 Fix/refactor fan curve table
    Table now managed by the configuration singleton, rather than the user-interface one.
    [configuration.h]
2022-08-01 Commit stranded changes to firmware
    Minor artifacts after firmware changes/refactor which were missed in previous commits?
    [app_background.c, led.c]
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2022-08-01 Fixed RGB pwm channel swap bug
    [led.c]
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2022-08-01 Name consistency fixes for LED queue event
    [app_background.c, app_task_led.c, app_task_supervisor.c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]
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2022-08-01 Fixed LED whitebalance tuning
    Firmware tweaks/fixes.
    UI updated and tested working.
    [configuration.h]
2022-08-01 PWM HAL frequency source tweak, changed APB2 to match APB1 freq
    Fixes off-by-half LED PWM frequency bug.
    Increase LED PWM frequency to resolve motion trail flicker.
    Corrected PWM Timer frequency used in prescaler calculation.
    [led.c, main.c]
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2022-08-01 Invert camera shutter release IO to match newly installed opto
    [app_times.h, shutter_release.c]
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2022-08-01 Fixed 'missed last iteration; bug in movement interpolation engine
    Resolves issue where moves occasionally miss the last percent or so of the target, leading to tiny inter-move jerks or accumulation of positional error.
    [path_interpolator.c, user_interface.c]
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2022-08-01 Start rework of motion ID system to 'timestamp offset' system
    Structure refactor and naming changes, small prep work.
    [app_task_motion.c, app_task_supervisor.c, path_interpolator.c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]
2022-08-01 Minor correctness fixes for updated path interpolator implementation
    [app_task_motion.c, app_task_supervisor.c, path_interpolator.c]
2022-08-01 UI codec cleanup and small fixes relating to pathing refactor
    [app_task_motion.c, path_interpolator.c]
2022-08-01 Refactor LED animation/fade handling to use 'global timestamp' method
    Matches newer 'global offset in milliseconds as the ID' approach used with movements to reduce barrier/sync style event issues.
    [app_task_led.c, path_interpolator.c]
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2022-08-01 Fixed bug affecting change-mode homing moves not flagging completion
    [app_background.c, path_interpolator.c]
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2022-08-01 Firmware spelling/grammar/lint corrections
    [configuration_types.h]
2022-08-01 Fixed regression in demo sequence mode introduced during sync refactor
    [app_task_supervisor.c]
2022-08-01 Set the LED PWM duty cycles to 0 during init
    Prevents default 50% duty cycle surviving to an operational mode where the driver is enabled and the led goes white!
    [led.c]
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2022-08-01 Clearpath driver attempts to detect missing servo via HLFB updates
    [app_times.h, clearpath.c]
2022-08-01 Disconnection of any enabled servo triggers error recovery
    [clearpath.c]
2022-08-01 Assert error messages are cached in RAM across reboot, reported to UI
    Improves troubleshooting ergonomics when programmer isn't attached/breakpointed in the assert handler!
    [app_hardware.c, main.c, user_interface.c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]
2022-08-01 Use shorter msgID's for reduced packet sizes
    Packet names don't need to be human readable anymore
    [user_interface.c, user_interface_msgid.h]
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2022-08-01 Increased effector speed limit and spline distance sampling count
    Speed checks function properly now, and higher resolution sampling of complex geometries don't incur problematic CPU load, so increase the resolution and speed limit.
    [app_times.h]
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
